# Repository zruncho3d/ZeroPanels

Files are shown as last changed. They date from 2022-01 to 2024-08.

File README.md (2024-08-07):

# ZeroPanels: the sealed, snap-in printer enclosure

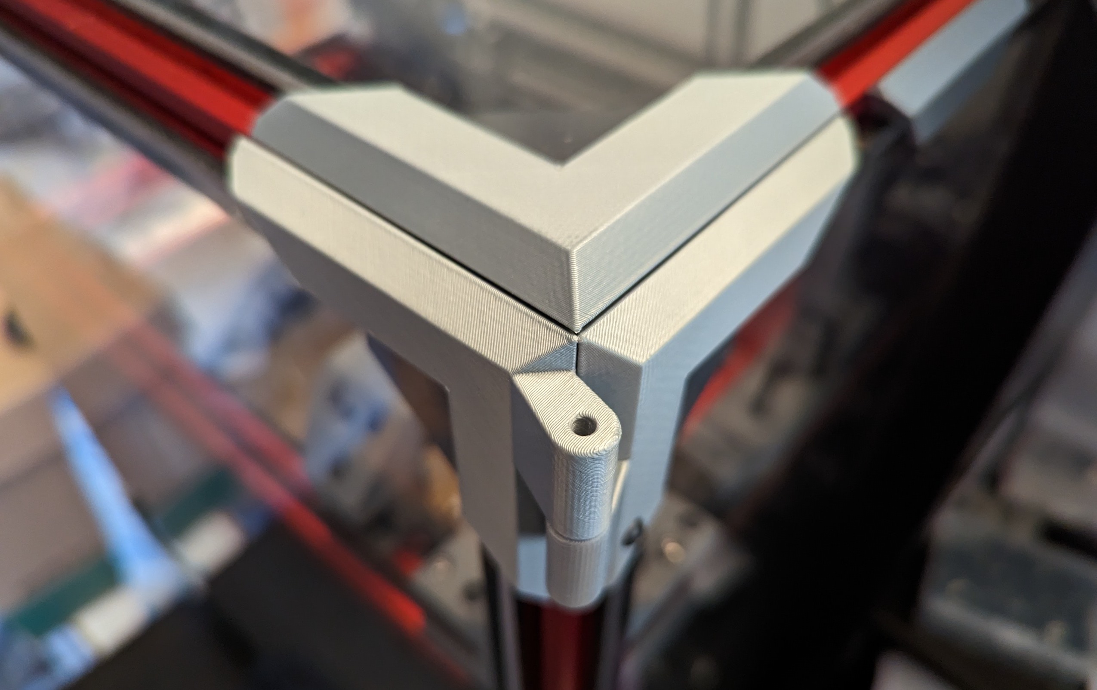
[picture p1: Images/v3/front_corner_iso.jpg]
Iso


**ZeroPanels** is an enclosure design for [Printers for Ants](https://3dprintersforants.com) which makes panel insertion and removal really, really, ridiculously easy.  

The design uses uses screw-less, nut-less, magnet-less, low-infill, 3D-printed clips... and it works with most 1515-based printers, including [Voron Zero](https://vorondesign.com/voron0.2)* (see Compatibility Notes below), [F-Zero](https://github.com/zruncho3d/f-zero), [Tri-Zero](https://github.com/zruncho3d/tri-zero), [Double Dragon (X0)](https://github.com/zruncho3d/double-dragon), [Micron](https://github.com/hartk1213/Micron), [Salad Fork](https://github.com/Yeriwyn/Salad_Fork), [Crucible](https://github.com/Maverick-3D/Crucible), and more.  

**Are ZeroPanels for me?** If you expect to build your printer, then never maintain it or mod it... *move along; these aren't the panels you're looking for*.

But if you've ever had to do maintenance on a printer, or really just enjoying modding and tweaking, then easy panel removal is a godsend, and worth a bit of filament, some tape, and a few magnets.

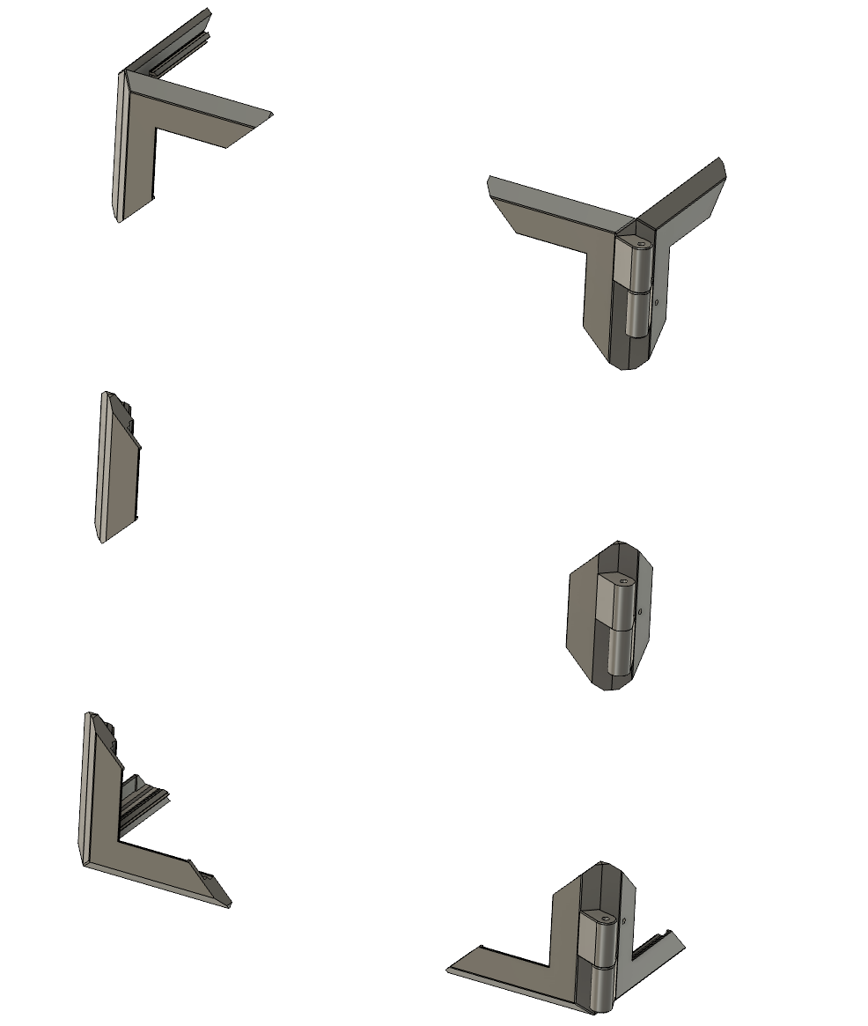
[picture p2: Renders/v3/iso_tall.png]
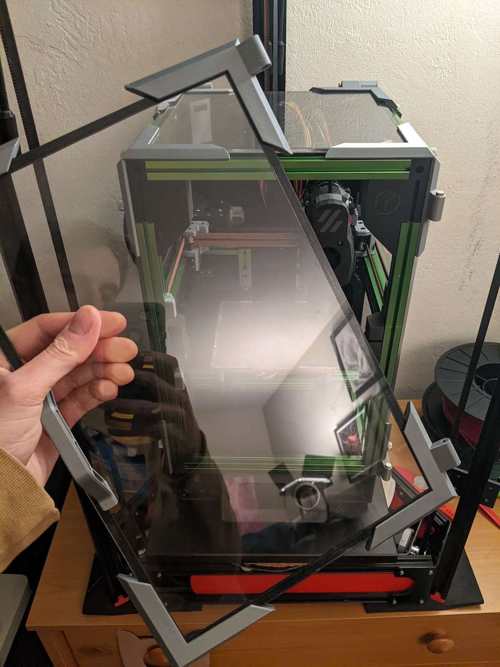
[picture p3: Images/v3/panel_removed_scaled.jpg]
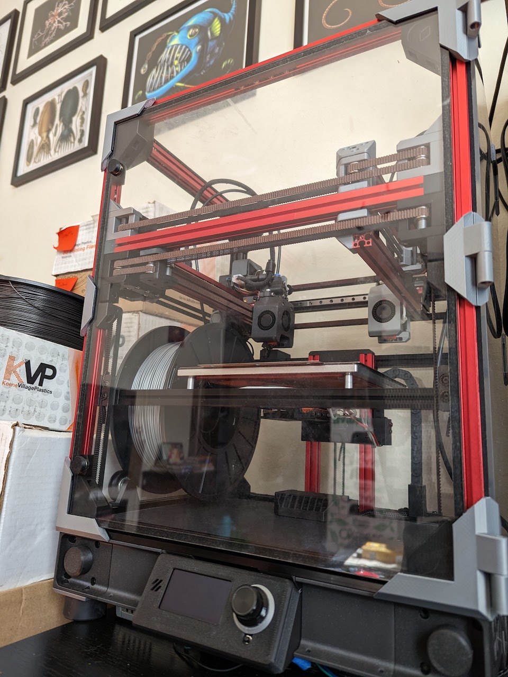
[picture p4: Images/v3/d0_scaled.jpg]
|  |  | 
| - | - | - |
| CAD Render | Zruncho's [Tri-Zero](https://github.com/zruncho3d/tri-zero) + [BoxZero](https://github.com/zruncho3d/BoxZero) w/ZPv3 <p>showing easy door removal and top hinge | Zruncho's [Dueling Zero](https://github.com/zruncho3d/DuelingZero) w/ZPv3 <p>and optional midclips|

**Version 3 adds many meaningful improvements:**
* new "one size fits most" design fits a broader range of panel sizes out-of-the-box
* no need to cut foam tape on a diagonal anymore
* new hinge parts support magnetic and screw-based hinges
* new optional screw lock for hinge bases
* new optional midclips ensure a tight fit with larger panels (like Micron+, Tri-Zero+, Dueling Zero, and others)
* new easier-to-edit, simplified Fusion 360 CAD

The minor downside is that VHB tape is now on the BOM.

[See this video](https://www.youtube.com/watch?v=6F5wUP4zZDg) for an explanation of what's new, with the v3 enclosure on [Dueling Zero](https://github.com/zruncho3d/DuelingZero).

This video is probably the best way to understand what they're like and whether they're for you.

## [> > > Watch v3 update video!](https://www.youtube.com/watch?v=6F5wUP4zZDg)

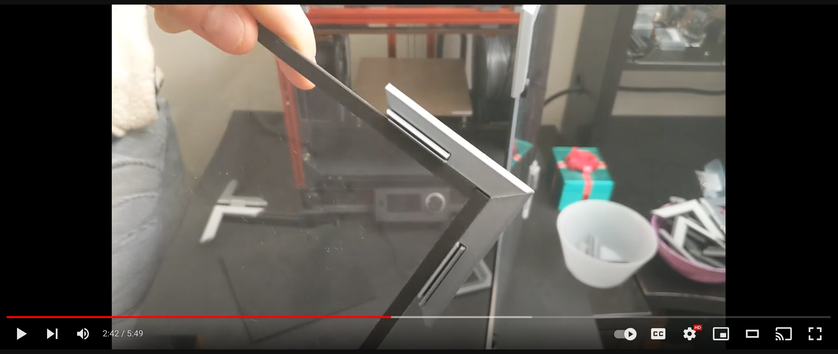
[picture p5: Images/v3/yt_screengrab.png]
(https://www.youtube.com/watch?v=6F5wUP4zZDg)


## [> > > Older v1 video shows fast insertion and removal!](https://www.youtube.com/shorts/L3nBHkO4VzE)

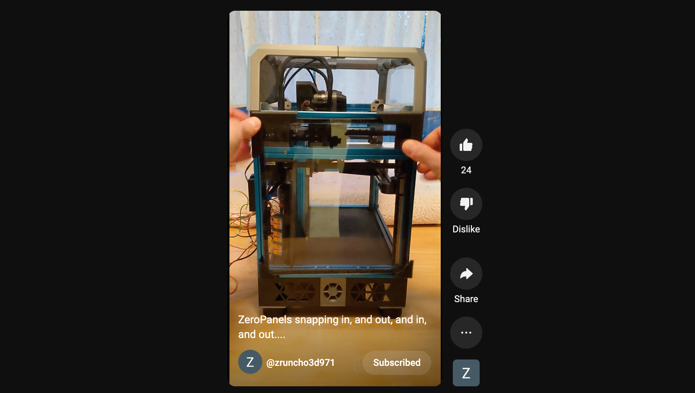
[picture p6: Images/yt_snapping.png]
(https://www.youtube.com/shorts/L3nBHkO4VzE)


## Updates
* 2023-03-05 v3 Release!
* 2022-12-13 v3 Beta program begins on DoomCube Discord
* 2022-04-18  ZeroPanels motivate [BoxZero](https://github.com/zruncho3d/boxzero), a fully-boxed V0 option.
* 2022-03-03 Tecnologic shares ["Tecnologic-style" ZeroPanels](https://github.com/Tecnologic/ZeroPanels/tree/main/Mods/tecnologic/FlyingZero300) for [F-Zero](https://github.com/zruncho3d/f-zero), which have a larger corner size, as well as optional inner parts, and cover all sides.  They're really nice.  They influence v3 and BoxZero.
* 2022-01-23 Public release of original V1 ZeroPanels, which are intended mostly for just the left and right sides of a printer, and assume a tophat on top and a default V0 hinged front panel.

## Why ZeroPanels?

**No !@#$ing screws and nuts.** A default V0 enclosure (just left & right) requires 24 screws and nuts. Even with [NoDropNuts](https://github.com/zruncho3d/f-zero/tree/main/STLs/NoDropNuts) to hold the nuts in place, having to unscrew a bajillion screws to remove one panel - and then screw them all back in again - is not fun.

**Mind the gap.** Many [Printers for Ants](www.3dprintersforants.com) need an extra mm to clear an MGN7 carriage (17mm wide) when mounted inside a 1515 extrusion.  You can solve this problem by printing thicker clips and using foam tape, but if you’re going to reprint enclosure parts… you might as well avoid the pain of all those screws too.

**Seals tight.** This gap is closed by foam that you add to the panels, and the extrusion clips gently press the foam against the panels.  Speaking of which...

**Shut the front door.** ZeroPanels are sealed by default, including the front door.

**Bye-bye, tophat.**  Easily add a top-hinge panel to replace a tophat on for fully-boxed printer mods like [BoxZero](https://github.com/zruncho3d/boxzero).

**ZeroPanels FTW.**  There’s more thought and work in these little parts than you might realize.

## Bill of Materials

| Part/Material | Description | Amount | Link | Note |
| - | - | - | - | - |
| Filament | Something strong and slightly flexible | - | - | Tested with ABS, though PETG probably will work, too.  PLA is probably not a good fit here. |
| Foam Tape | 3mm or 1/8" Adhesive-backed Foam Tape | Enough to cover all panel edges | [example (Amazon) ](https://www.amazon.com/gp/product/B08MTXJBR5/ref=ppx_yo_dt_b_search_asin_title?ie=UTF8&psc=1) | The Yotache brand is nice, because it doesn't show lines on the adhesive side through the acrylic, unlike others. |
| Tape | Double-sided VHB tape (1mm-ish) | Some | [example (Amazon)](https://www.amazon.com/gp/product/B09R5ZF8XZ/ref=ppx_yo_dt_b_asin_title_o01_s00?ie=UTF8&th=1) | Doesn't need to hold *that* well; non-genuine VHB is probably fine. |
| Magnets | 6mm dia x ~3mm depth "V0 standard" magnets | 6 per hinge pair | Some | See "Choosing a Hinge" below |
| Screws | M3x35 SHCS/BHCS | 2 per hinge pair | Link | See "Choosing a Hinge" below |
| Screws | M2x12 self-tapping screw (or M2x10 in a pinch) | - | (optional) 1 per hinge | Optional screw lock.  Can also drill out the hole and use an m3 screw too, if the hole strips, or you just want an m3. |
| Nuts | M3 regular or Nylock nut | 2 per hinge pair | Link | See "Choosing a Hinge" below |
| Panels | 3mm | Depends | - | These should be sized for ~6mm beyond the inner frame width.  For example, on a V0, 200mm + 6mm * 2 --> 212mm width.  *Note*: the front door becomes the same size as the side panels, so a V0 panel kit with tophat needs a 9mm shave on the top to fit here.|

**Choosing a Hinge**: magnet or screw?  You can do one of each; Zrucho's preference is a screw-hinged top and magnet-hinged front.  You can even skip a top hinge and just use a snap-in top panel, especially if you want to flip your printer and have it sit on a flat surface frequently.

The magnet hinge enables you to grab the front panel, lift up, and remove it entirely.  The screw option enables you to tighten the screws, so that the top panel holds in place vertically, for extruder access or filament changes.

If you want a nice strong front-door close, then add 2-8 optional door magnets. The printed parts match the ZeroPanels offset, but also give a more powerful seal.  The front-door bits require a few extra parts:

| Part/Material | Description | Amount | Link | Note |
| - | - | - | - | - |
| Screw | M2x10 self-tapping screw | - | 1 per unit | Longer lengths can typically be cut down to size with strong wire cutters. |
| Screw | M3x6 FHCS | - | 1 per unit | |
| Tape | Thin double-sided tape, 1/4" / 6mm wide | - | Enough to cover one magnet per unit | Cut any size width you have to size. |
| Magnet | 1/8" thick, 3/8" diameter countersunk ring magnet | - | 2 per unit | Choose your preferred size |
| Magnet | 1/8" thick, 1/2" diameter countersunk ring magnet | - | 2 per unit | Choose your preferred size |

## Printing Tips

The unusual 45-degree orientation is what makes these possible.

For **non-hinge** parts:
* 0% infill (minimum), 2 perims (minimum), 2 bottom layers, 5 top layers, 0.6 forced width, 0.2 layer height

The wider extrusion width helps with the overhangs.  However, if you get too much corner curl with the wider width, try 0.45 or 0.5 width instead, possibly with an extra perimeter, and/or reduce the layer height to 0.16mm.

For **hinge** parts:
* Same params, except use 16% infill (minimum); extra perims may improve hinge strength too

Bed adhesion is important for a cantilevered part like this.  Consider all of these:
* a hotter heated bed
* a properly prepared PEI surface (soaped, scuffed, iso'ed)
* extra first-layer squish
* an adhesion aid like Vision Miner Nano
* brim, if still stuck

If there's an interference with the extrusions, then you'll need to fix it in CAD beforehand (using a press-pull operation is easy enough...) or use flush cutters after.  Sorry, but generating and orienting versions of every part for every printer is a maintenance burden.

Get the settings right, and each part should look perfect, even when printed at the flowrate limit of the hotend.  The sample parts below show v1 parts in KVP Stellar Black ABS, printed at 235C on an [F-Zero](https://github.com/zruncho3d/f-zero).

Print Sample

## Instructions

### Required Reading: understanding the thickness setting

**Always print and assemble a test panel first, because component thicknesses vary.**  

Acrylic panels, extrusions slots, foam tape, and VHB tape all vary slightly in thickness, as does each printer.  You want to ensure that these parts work for your printer, *before* printing a full set.

The default panel set assumes these sizes:
* VHB tape thickness: 1.1mm
* acrylic panel thickness: 2.9mm
* foam tape thickness: 3.0mm

This stack needs a tiny bit of squish to form a good seal.   If that stack is too skinny for the plastic part, an air gap will result.  If that stack is too thick, the tape near the hinges may separate over time, and a gap may form in the center of the panels due to bowing.  In a hot chamber, your panels might even set into a bowed position.  

By default, the stack assumes a 7.0mm stack thickness, squeezed down to 6.7mm, ensuring about 0.3mm of squish.

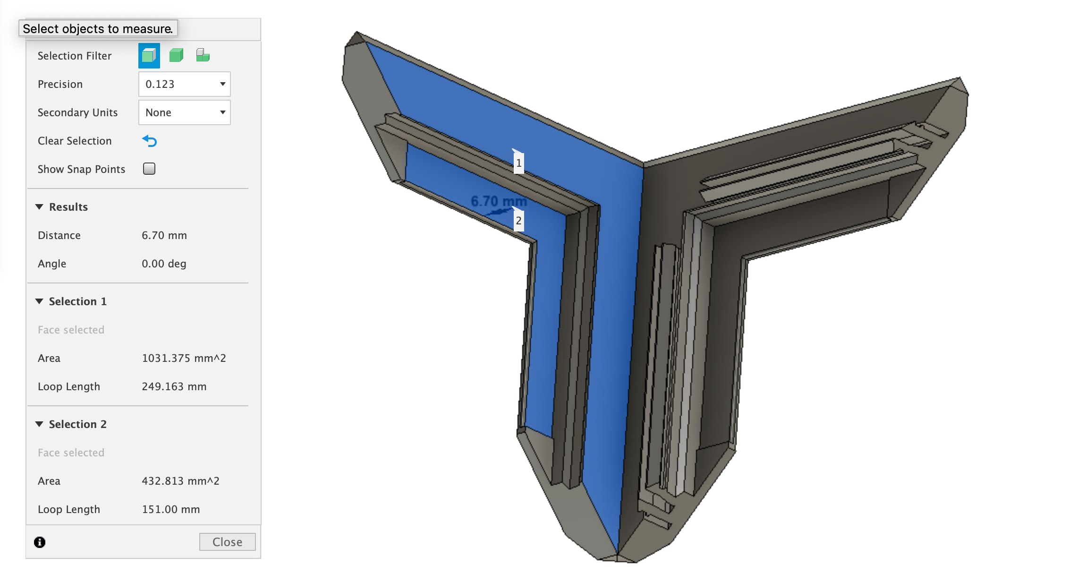
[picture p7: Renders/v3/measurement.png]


These numbers are based on the collected measurements from the many beta testers, in an attempt to provide a single reasonable default.

The amount of "extrusion grip" has been set similarly, to a size that should fit most extrusions and provide a reasonably satisfying, audible click, especially with LDO and MakerBeamXL extrusions.  Misumi are known to have wider slots, but you can somewhat account for this by offsetting the attachment of the corners to the panel, to effectively preload them, plus the screw locks for the hinges help here too.

If your component stack is less than 6.8mm or more than 7.2mm or so, then you're more likely to benefit from a custom size. However, if you need a size tweak, it's a straightforward change in the Fusion 360 CAD, as noted below.  **Try it first.**

### Print and assemble a test panel

#### Print and prep corners

Print 4 normal corners, using the settings above.

For each piece, cut out VHB to fit, with 90 degree cuts only, for all areas that will touch the panel.  Use two pieces for the L shapes and 1 for the straight-through mid-pieces, as shown below.

Push the tape downwards, and ensure it sits perfectly flat, or reapply the tape and try again.  A printer spatula works great for this purpose.  Looks like this:

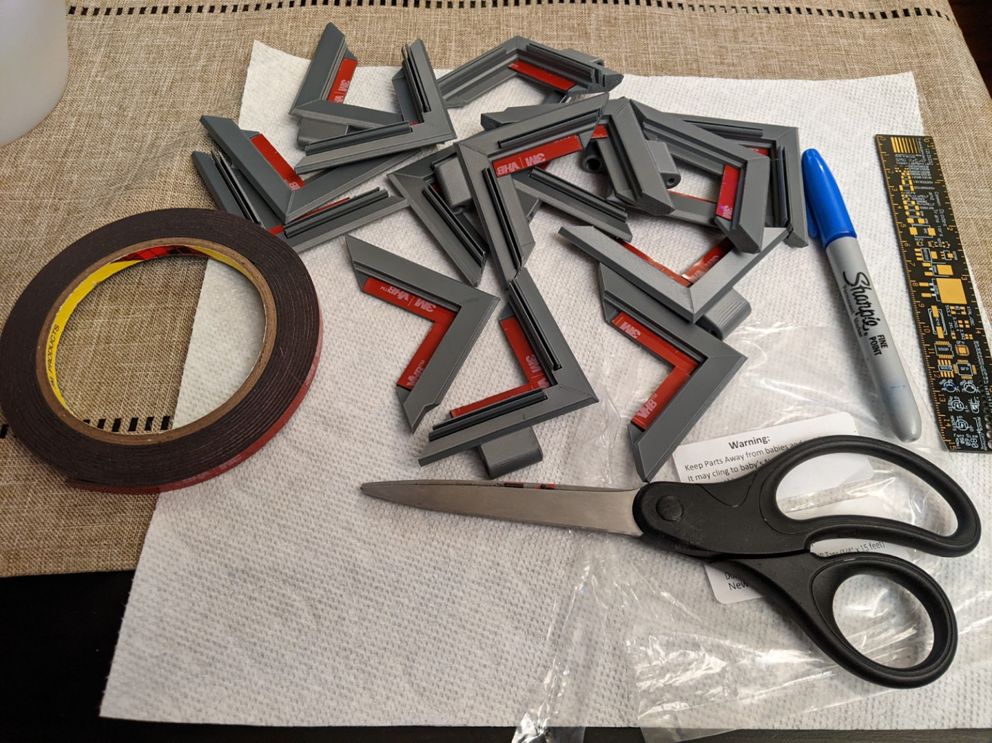
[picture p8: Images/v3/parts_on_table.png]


#### Prep panel with foam tape

You can do this while your parts are printing.

Remove a panel’s length of foam tape.  Get it started at one end, then *very gently* apply a bit of tension on the tape; run your finger along the panel edge and the tape edge.  You can get a perfectly-straight application with this technique, and by not pulling too hard, you prevent ugly stuff from showing on the tape's underside.  Just make sure everything overlaps.  

Repeat for the other 3 parts to complete a panel.

Make sure to remove the acrylic panel backing first!  You can remove just the edge part to keep the panel pristine.

Then put a book on top and let it sit foam-down for a bit.  Otherwise, expect that the tape might peel up near the edges, where you’re likely to have touched it the panel with your finger oils.  You want the tape to set a bit.

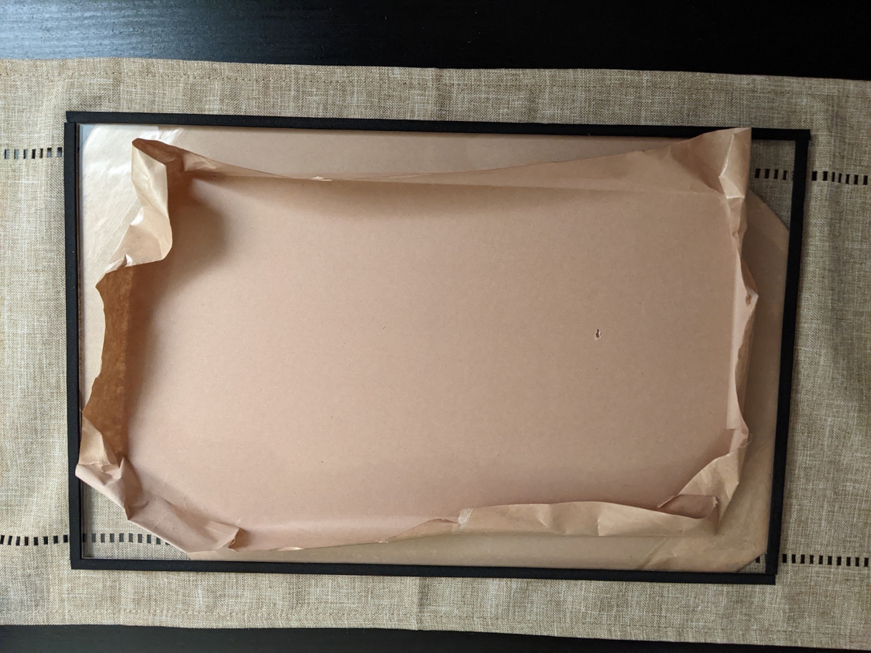
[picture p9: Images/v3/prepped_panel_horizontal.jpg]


#### Pre-test the panel

Make sure there are no occlusions before trying this - that is, there are no clips interfering with printed parts, and no nuts where the panels will insert.  Trim the clips if there are any occlusions.

Add all 4 clips with the red VHB backing still in place, to confirm that the stack height is about right.  Make sure the panel grips into the extrusion slots. The panel should hold securely, but remove easily when you push out from the inside, one corner at a time.  It's kinda like removing car interior pieces with plastic clips.  

Now, do the real test.

#### Assemble the panel

Remove the VHB's remaining red backing on the 4 clips. This step can be surprisingly hard if the backing sticks well to the tape itself.  Here's a protip: using a thin flat printer spatula, separate a corner of the backing from the tape.  As soon as you have a little triangle to grab, use needle-nose pliers to grab the tape and slowly peel back.  You can use this trick to avoid disturbing the VHB and having it peel away from the part.

Next, secure one plastic corner to a panel corner.  Mark the corner, say, with a Sharpie on the inside.   Squish it HARD.  Align the panel to the printer.  Do the same for the opposite corner, being careful to align it all to the extrusions.  Squish it hard.  Then add the other 2 corners in place.  To help ensure the VHB sticks as well as possible, you can pop off the panel and have some books weigh it down.  Make sure it has time to set before doing insertion/removal testing.

#### Check the fit

Look from the side, using a phone flashlight, to ensure no air gaps are present.  The panel should seal.  If it bows outward, consider using the optional mid-clips and mid-hinge for additional hold.

See if the amount of snap feels right.  See whether the assembled panel holds steady once inserted, and whether it removes with an amount of force that works for you.

**All good?**  Print the rest.

### Print the rest

#### Assembling magnetic hinges



These are simple, easy, and fast to build.

First, make a magnet pair for each hinge: literally, a pair of glued magnets with some CA glue.  It's out-of-chamber, so regular glue is fine.

Put a spot of glue into the hole on the fixed part, where the magnet pair will go; for the door, these would be on the right, and are the parts with a hole for an M2 locking screw.  Push the magnet pair in and make sure it sits flat.  Yes, a whole magnet sticks out.

Now, get the moving part, the one without a hole, with a deeper pocket.  Clean up the hole beforehand with a 6mm diameter reamer, end mill, or M6 screw.  Everything is glued here and non-critical, so a little looseness in the magnet pockets is fine; you just need the magnet to insert and remove easily, plus have space to act as a hinge.  Put a spot of glue in this part.  Then add a magnet onto the magnet pair of the fixed part from before, and press this into the pocket, just enough to become obscured.  Slide it out carefully, then press down all the way with a pen or other plastic thing that fits, until it sets from the glue.  

Test the hinge!  It should pop on and off without issue and rotate easily.  With two, the rotation will be even smoother.

#### Assemble the door

Assemble two hinge pairs and complete the right-side panel.  Attach the right-side panel and lock it in place with the M2 locks near the hinges.   Turn the screws until they hit the end and resist, but DO NOT strip them.  The screw locks don't need to be super-tight anyway; they're mostly preventing the panel clips from unclipping, vs actively pressing against the extrusion slot.  Worst-case, if you strip these, you can remove a chunk of panel clip, drill them out to m3, and have them mate to a nut in an extrusion slot.

Then assemble the door panel, ensuring that you use smooth corners, and add it.  You *can* use the panel clips everywhere, including as a door closure, but given the high cycle life there, magnetic feels right... it has an infinite cycle life.

The door should pop on and off easily.  To reattach, push the door against the front, then let it fall down into place.

Once it's in place, consider printing and attaching the optional-but-recommended magnet bumps, which cover up cylinder or ring magnets, and which grip tightly to the corresponding magnet receivers that clip into the extrusions.  The bumps attach using thin (0.1mm or so) double-sided tape.

Two magnet bumps on the left of the door is a good start, with others on top and side if you see air gaps or want a generally tighter seal.  Use more for bigger panels, too, especially for T0+ or D0-size printers.

#### Assemble a screw-based hinge (especially on top)

Similar steps here. The screw top will be exposed on the top side (assuming the door orientation), and a nylock nut goes into the pocket, and is hidden.  Tighten both screws fully only when the top and back are in place, along with the M2 screw locks on the top rear.

You can go tight enough for the hinge to hold vertically in place.

### Troubleshooting Tips

**Cooling a problem?**  Print the full plate or space out the parts on the plate.  Print thinner layers, print slower, and print cooler.

**Adhesion a problem?**  Add a brim, add more first-layer smush, print thinner layers, or use a bed adhesive.

**Strength a problem (breaking at layer lines)?**  Reduce cooling, add an enclosure, or jack up the print temp.  These are functional parts and should always be printed hotter if possible, for strength.

## CAD Notes

The CAD is designed to be understandable and modifiable, so you can do your own customizations, if not a CAD expert.

All sketches, operations, and construction planes are labeled.

Almost all dimensions of value are stored as parameters.  Here are the most useful ones:

`foam_tape_compressed_thickness`: adjust this from the default size for your stack
`no_grip_len`: increase if you want more length without a clip
`main_corner_len`: increase to 80 if you want a longer clip

Other params don't affect the corners, but make it easy to set the distances to match your printer, for easier CAD import.

Once you've made your adjustments, you'll need to export all bodies, reorient on the 45, and face all seams face backwards so that they end up hidden.

## Compatibility notes

(1) The latest [Voron Zero](https://vorondesign.com/voron0.2) (0.2) needs flat top chops on the corners for extrusion tophat compatibility (so that the clips don't interfere with the tophat plastic parts).  For compatibility with a full-height front, like those found in most V0 frame kits, you'd need to also mod the front clips a bit, since the plastic would be in the way of the top 9mm and bottom 9mm of acrylic panel.

(2) The original Dueling Zero README lists panels that are 9mm beyond the inner frame width, not 12mm.  To use these on D0, make sure to adjust the magic 'x' parameter and follow the note in the CAD, then export the parts you need.  If you go for normal-size frames, then ignore this message.

## FAQ

### What's the catch?

Because the clips enable the panels to float, the panels provide no rigidity benefit to the frame, just like [curtain walls](https://en.wikipedia.org/wiki/Curtain_wall_(architecture)) on modern skyscrapers.

However, because these panels aren't positively coupled to the frame, they may reduce noise, to make it less likely that they act as a speaker to amplify resonances.

We'll see about that one.

Another possible catch is that not every printer is dimensionally accurate, and that can affect how well the design works *for you*.  They're designed to account for variance in panel width, extrusion slot width, and panel thickness.  But if your printer prints bulges at the corners, for example, the clips may not work for you.

### Could I extend the design to fully cover extrusions?  Yes.
Yes, you could!  See the [Technologic-style version](https://github.com/Tecnologic/ZeroPanels/tree/main/Mods/tecnologic/FlyingZero300) for an example.

You'd have to think through the print orientation(s) though to fully reuse this profile.

### Can I do a double-panel version?  Yes.
Definitely.  You'd need to thicken the panels, but add an extra layer of VHB and another panel and make small mods and you may be able to do a simple double-panel setup.

## Credits

These parts are a spinoff from the [Tri-Zero](https://github.com/zruncho3d/tri-zero) project.

V3 credits:

Thanks to Grizzle357, sorkyl, Floaf, falo, SuperPringles, burningBeard, Ax4x Se7en, John, Kosh42EFG, schwaded, and Bacon for taking measurements that informed the parts here.  Thanks to chadonka for printing an entire enclosure on an in-progress D0!

V2 credits:

Unreleased, but inspired by Tecnologic.  The CAD got out of hand and needed to be redone properly, starting over from the first sketch.

V1 credits:

Thanks to Yeri, Speedy, Ericsson, RogueNeurons, Maverick, Sparkss, rok3, flyespresso, tecnologic, and Lowstream on the [DoomCube Discord](https://discord.gg/doomcube) for extrusion measurements.

Thanks to Ericsson, RogueNeurons, Maverick, Yeri, rok3, flyespresso, StoicHollow, Lowstream, and Tigran on the [DoomCube Discord](https://discord.gg/doomcube) for sharing test-print feedback!

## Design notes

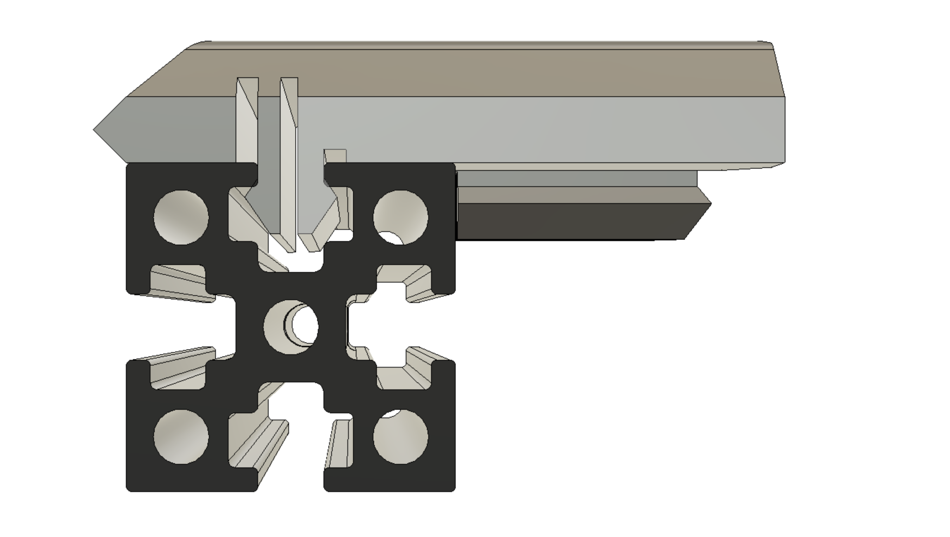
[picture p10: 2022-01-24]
Renders/side_view_perspective.png

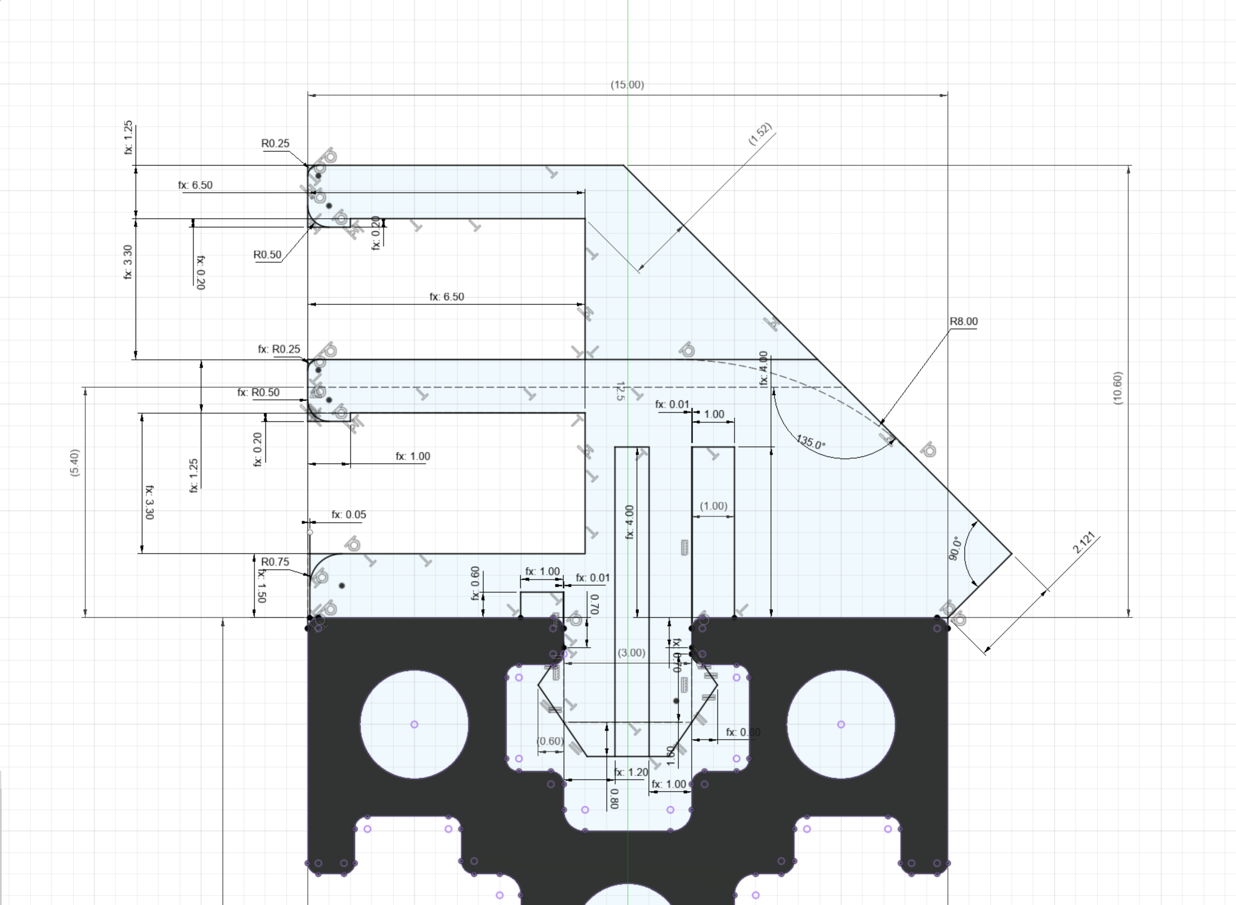
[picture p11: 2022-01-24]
Renders/sketch.png

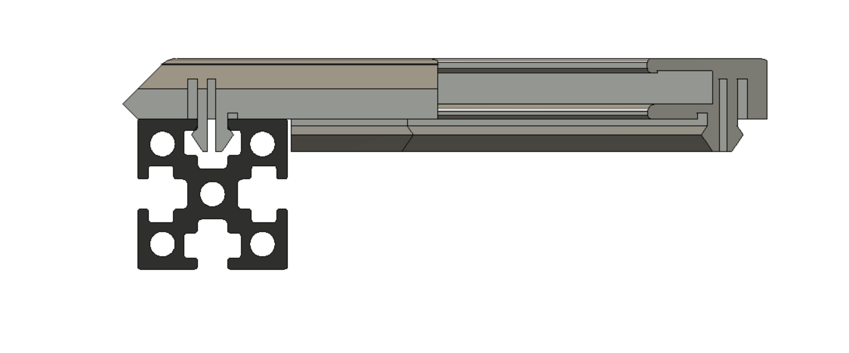
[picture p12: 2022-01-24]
Renders/side_view_ortho.png

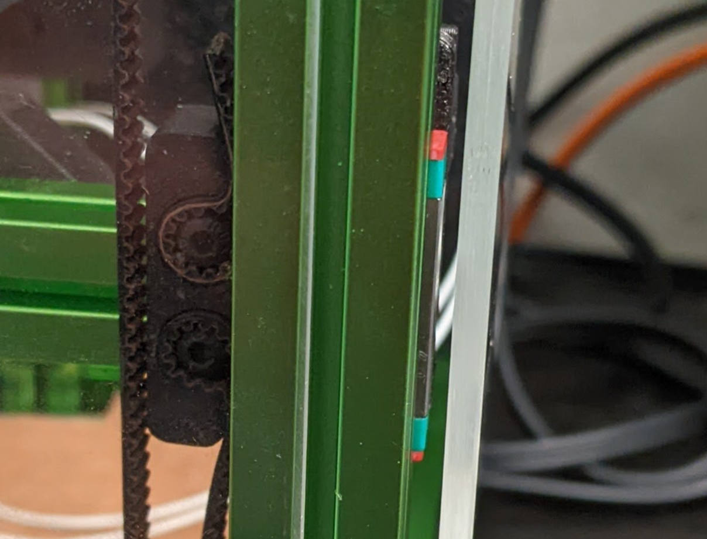
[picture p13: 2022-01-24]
Images/T0_filling_the_gap.png

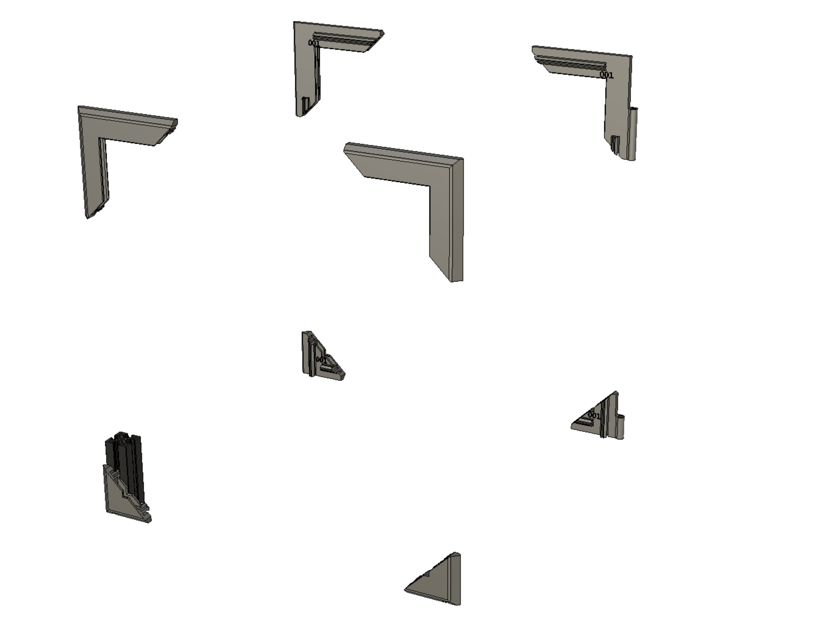
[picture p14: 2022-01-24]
Renders/all_in_iso.png

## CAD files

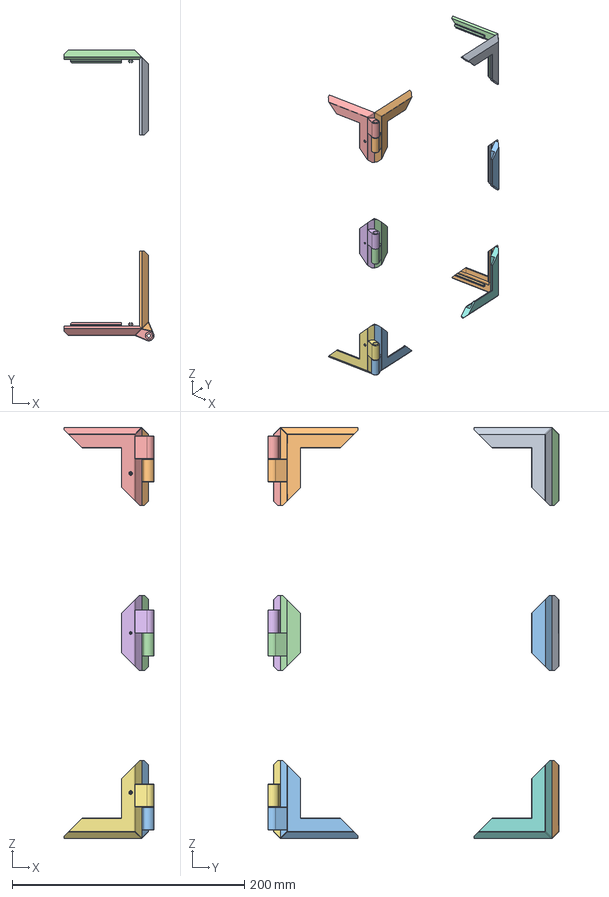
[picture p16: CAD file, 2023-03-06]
CAD/ZeroPanels_v3_2023_03_05.step
77.6 x 250.6 x 354.2 mm

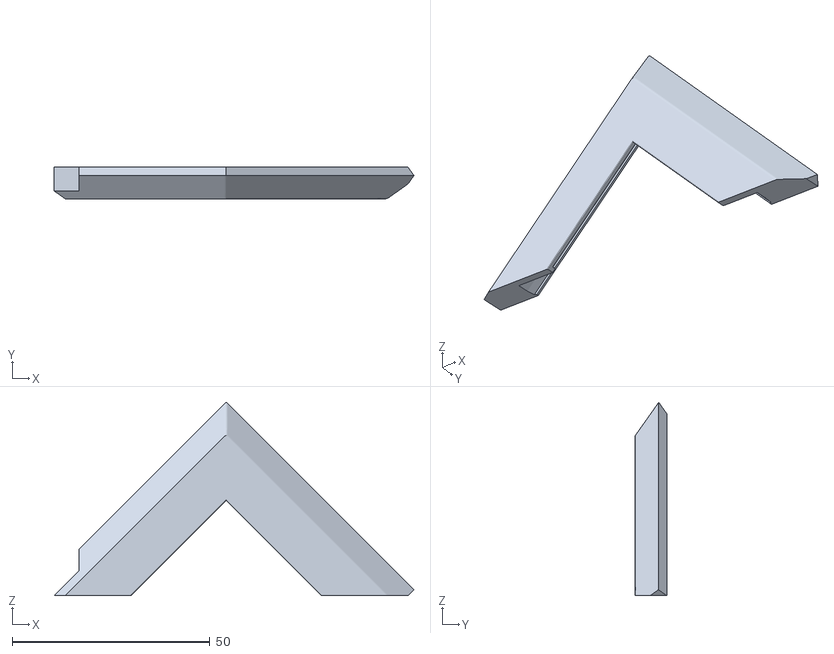
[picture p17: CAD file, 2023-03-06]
STLs/v3/optional/zp_smooth_bottom_12864cutout.stl
90.9 x 8.00 x 48.9

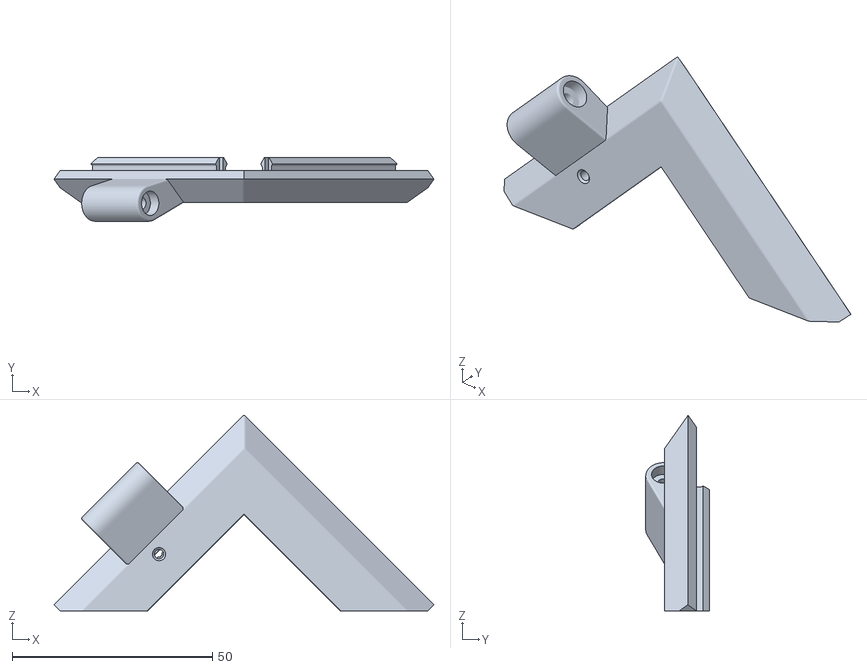
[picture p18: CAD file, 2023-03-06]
STLs/v3/zp_hinge_top_fixed_x2.stl
94.9 x 15.9 x 48.9

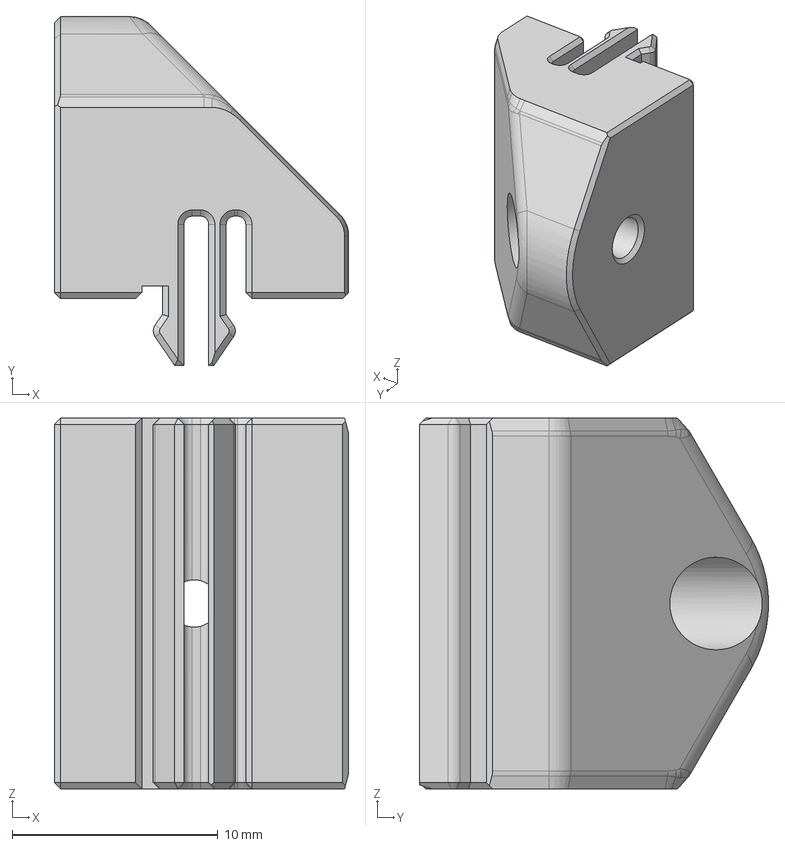
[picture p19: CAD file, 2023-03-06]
CAD/Magnet_Receiver.step
14.3 x 16.9 x 18.0 mm

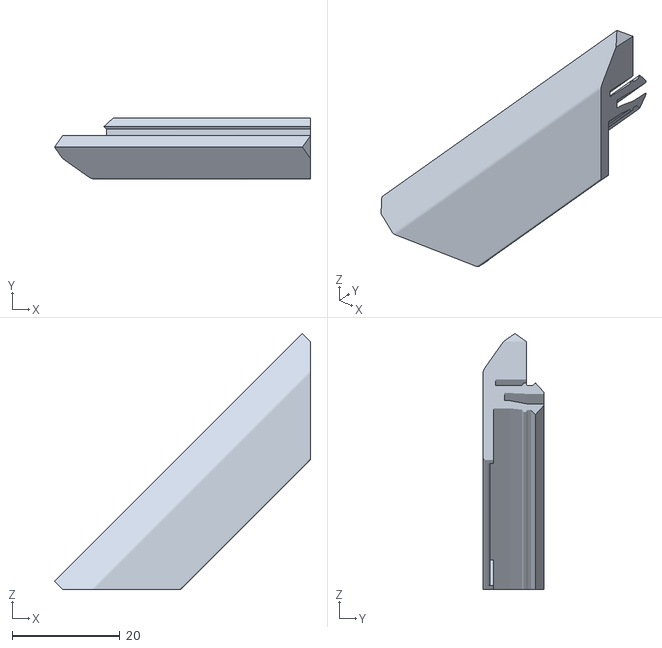
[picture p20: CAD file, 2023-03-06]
STLs/v3/optional/zp_midclip_optional_x5.stl
47.5 x 11.3 x 47.5

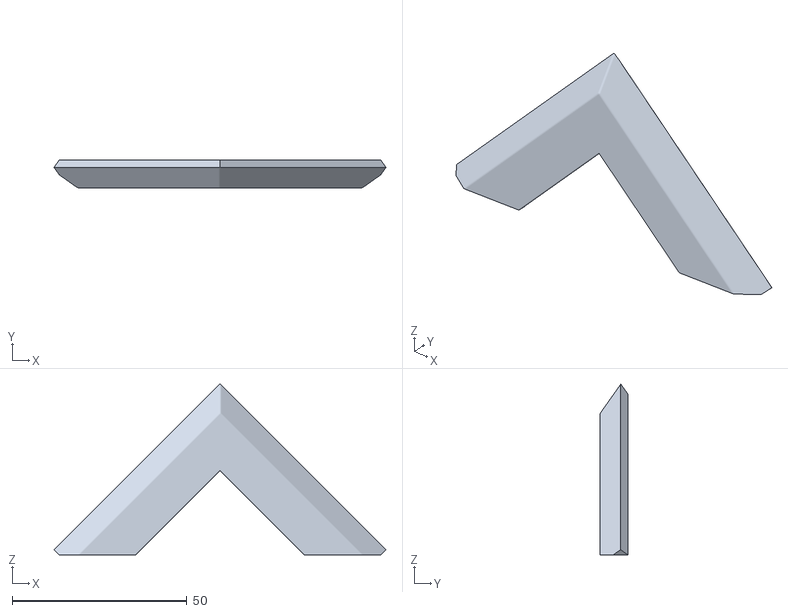
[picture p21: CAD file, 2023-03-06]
STLs/v3/zp_smooth_x2.stl
94.9 x 8.00 x 48.9

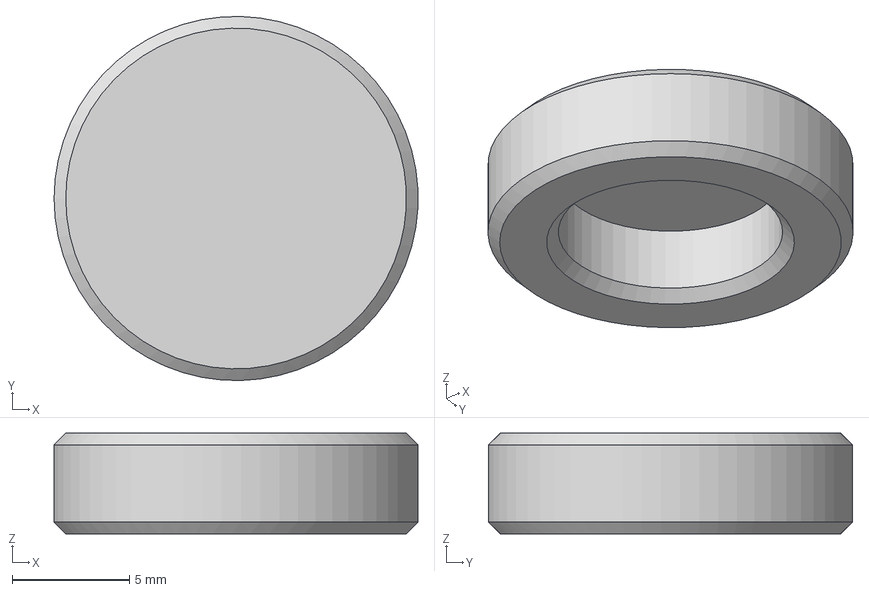
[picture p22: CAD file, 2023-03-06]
CAD/Magnet_Bump.step
15.5 x 15.5 x 4.30 mm

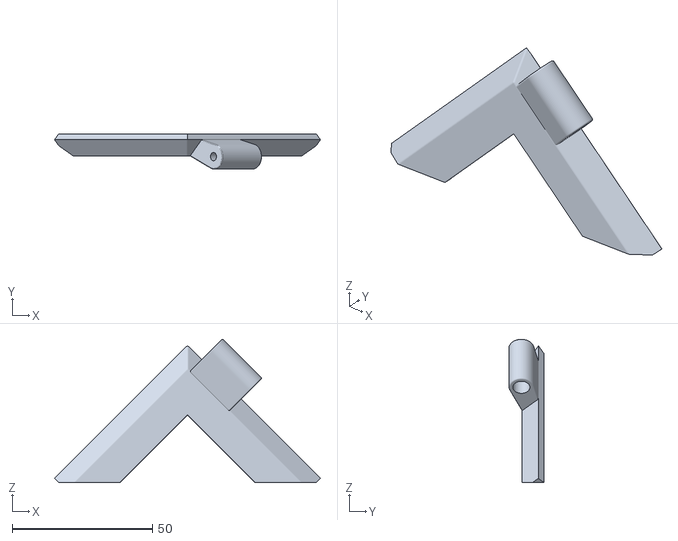
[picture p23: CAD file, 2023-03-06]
STLs/v3/zp_hinge_top_moving_x2.stl
94.9 x 12.6 x 51.2

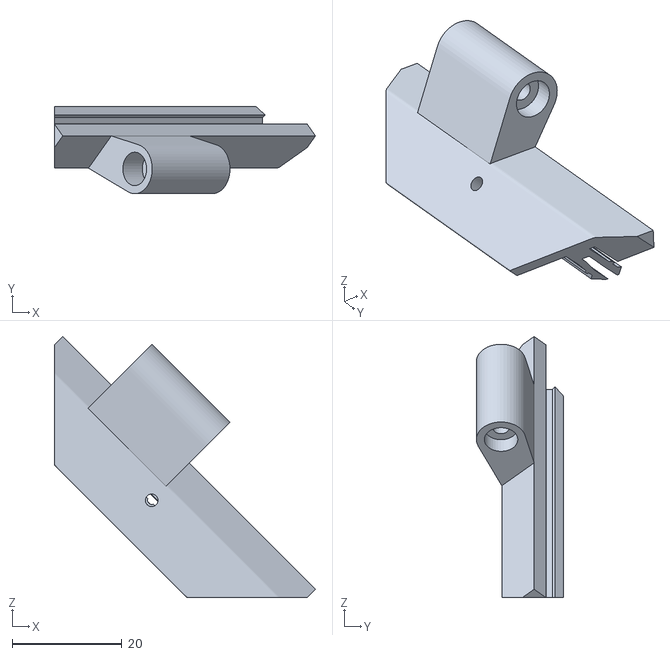
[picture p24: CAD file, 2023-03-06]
STLs/v3/optional/zp_hinge_middle_fixed_optional.stl
47.5 x 15.9 x 47.5

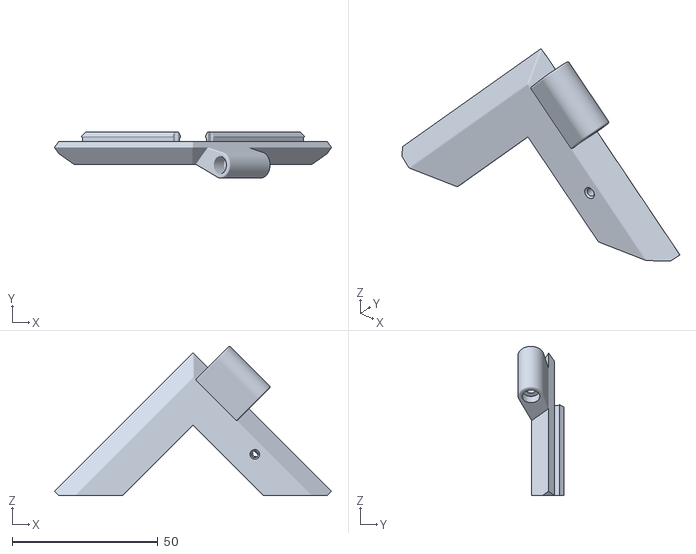
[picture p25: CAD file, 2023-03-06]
STLs/v3/zp_hinge_bottom_fixed_x2.stl
94.9 x 15.9 x 51.2

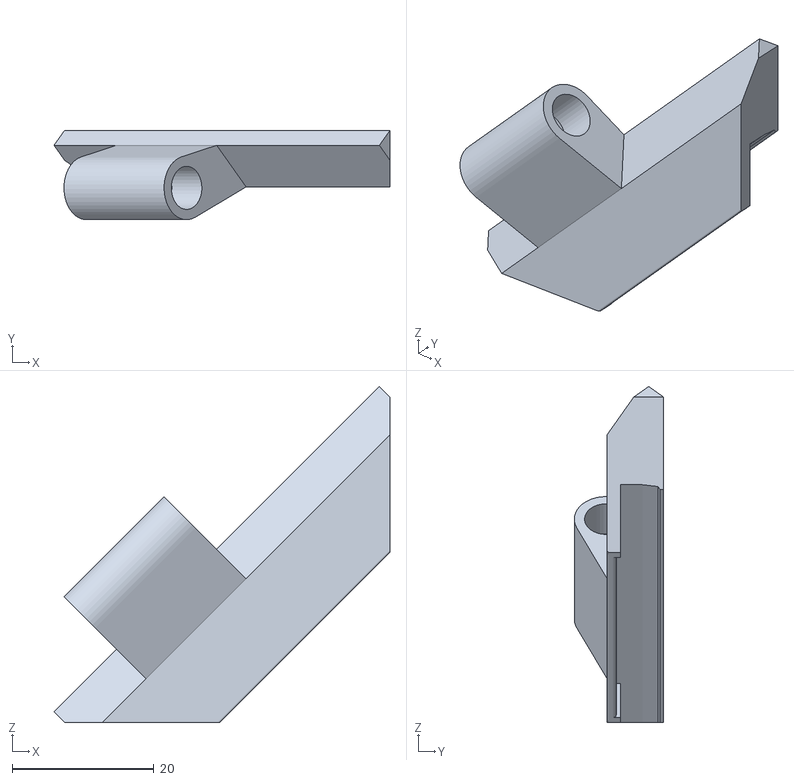
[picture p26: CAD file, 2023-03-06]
STLs/v3/optional/zp_hinge_middle_smooth_optional.stl
47.5 x 12.6 x 47.5

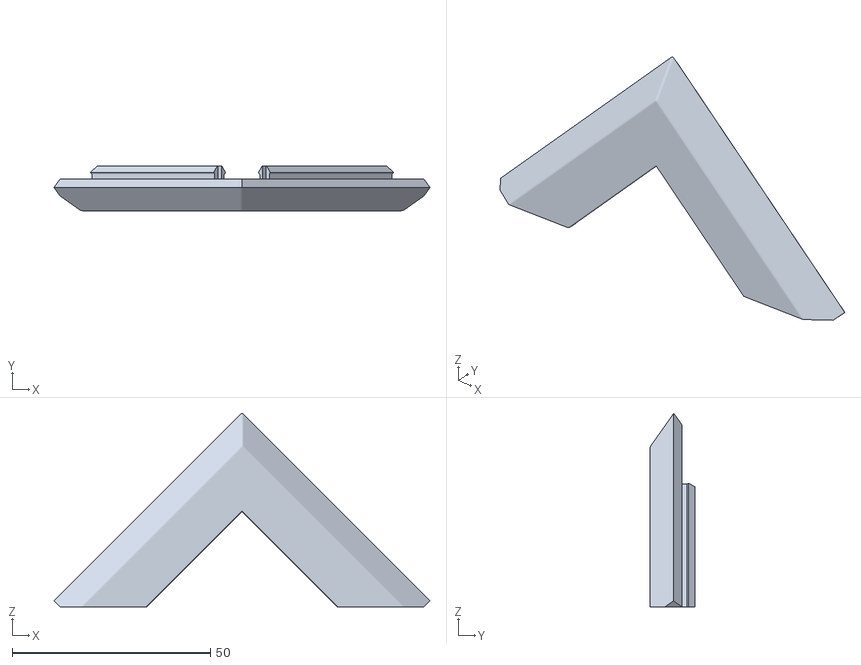
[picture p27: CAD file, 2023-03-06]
STLs/v3/zp_clip_x8.stl
94.9 x 11.2 x 48.9

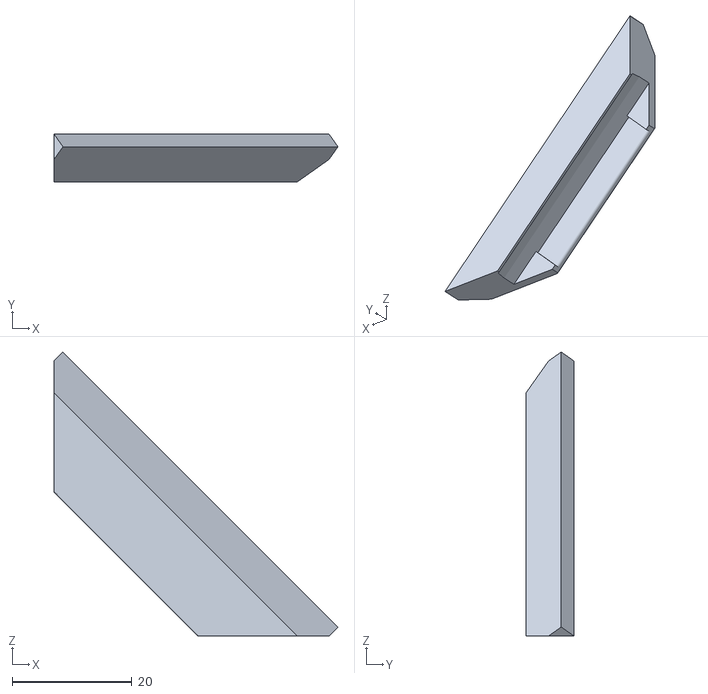
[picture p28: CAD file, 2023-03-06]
STLs/v3/optional/zp_midclip_smooth.stl
47.5 x 8.00 x 47.5

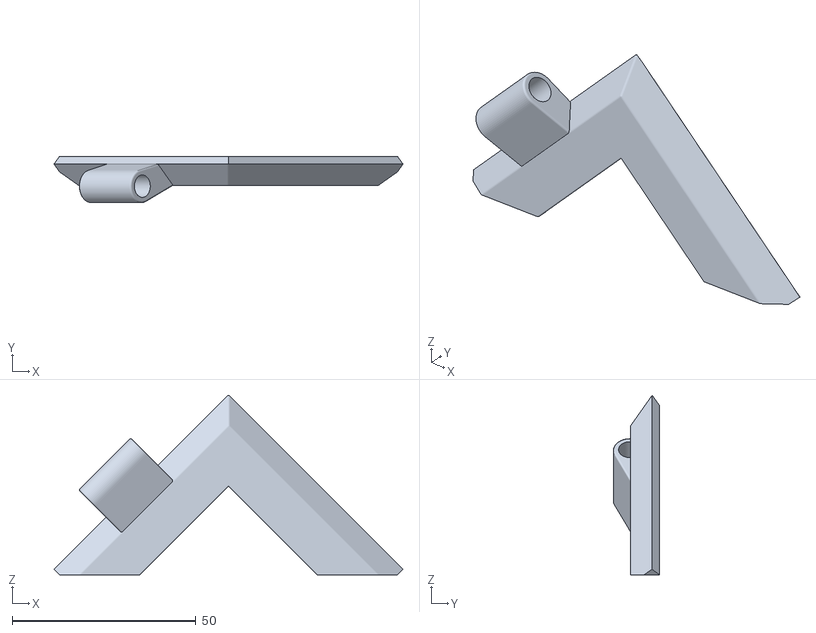
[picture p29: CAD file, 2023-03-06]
STLs/v3/zp_hinge_bottom_moving_x2.stl
94.9 x 12.6 x 48.9

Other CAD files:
STLs/v3/optional/magnet_receiver.stl
STLs/v3/optional/zp_hinge_bottom_moving_12864cutout.stl
STLs/v3/optional/magnet_bump.stl
STLs/Archived/Parts/General/General_015_Left_Front_Top_Right_Rear_Top_Clip_x2.stl
CAD/Archived/ZeroPanels_2022_01_23.f3z
CAD/Magnet_Bump.f3d
CAD/Magnet_Receiver.f3z
CAD/ZeroPanels_v3_2023_03_05.f3z
STLs/Archived/Parts/General/General_001_Left_Front_Bottom_Right_Rear_Bottom_Clip_x2.stl
STLs/Archived/Parts/General/General_001_Left_Front_Top_Right_Rear_Top_Clip_x2.stl
STLs/Archived/Parts/General/General_001_Left_Rear_Bottom_Clip_x1.stl
STLs/Archived/Parts/General/General_001_Left_Rear_Top_Clip_x1.stl
STLs/Archived/Parts/General/General_001_Right_Front_Bottom_Clip_Hinge_x1.stl
STLs/Archived/Parts/General/General_001_Right_Front_Top_Clip_Hinge_x1.stl
STLs/Archived/Parts/General/General_015_Left_Front_Bottom_Right_Rear_Bottom_Clip_x2.stl
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

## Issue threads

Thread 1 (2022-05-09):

Any way to mount the back panel using these parts?

bassamanator, 2022-05-09:
I'd like to mount my Voron 0.1 back panel using this design, but it seems this will only work for the size panels?

Interesting design. Thanks!

zruncho3d, 2022-08-30:
(just seeing this now)

You can lift the back panel up and it should still seal, at least using Tecnologic-style panels (a larger variant I really like).  More here:
https://github.com/zruncho3d/BoxZero

You may need to add some foam tape to the back, by the motors/umbilical plate though, but you shouldn't need a larger plate.

Closed 2022-08-30.

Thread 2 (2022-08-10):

Insulation

taihon, 2022-08-10:
Hello. First of all - thank you for this mod :) It's fast to print and beatiful to look at.
In the FAQ section you've mentioned "clips enable the panels to float". How would i go about insulating v0 chamber then?

taihon, 2022-08-10:
To anyone who comes here in the future - we're supposed to put foam tape on panels inbetween clips, as usual.

zruncho3d, 2024-08-07:
Yep

Closed 2024-08-07.

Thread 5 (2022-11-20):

Can't slice the files.

Neiizo, 2022-11-20:
Well.... I have posted this with no text by mistake...
I wanted to print this, but for some reasons, I cannot slice the part. I am trying to print the v0 15 parts plate. I am using superslicer. I have heard on discord I am not the only one having this issue. any clue why?

EDIT: I have found the culprit: I cannot set 1 perimeter at 0.7mm wall thickness

Neiizo, 2022-11-20:
Well.... I have posted this with no text by mistake...
I wanted to print this, but for some reasons, I cannot slice the part. I am trying to print the v0 15 parts plate

Closed 2024-08-07.

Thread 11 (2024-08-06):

2020 slot 5 version?

Jomik, 2024-08-06:
Hey! This looks really awesome, would love to use it on my printer.
It is a 2020 with a 5mm slot from [motedis](https://www.motedis.dk/en/Aluminium-Profile-20x20-I-Typ-slot-5).
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

I looked into the CAD, but sadly I can't really see a good way for me to adapt this? Can you enlighten me on what I would need to change? Or if it's an easy change for you, I'd love a version! :)
I hoped for it to just be two variables 🙈

zruncho3d, 2024-08-07:
Newer CADs of mine explicitly parameterize the extrusion size, but this one predates that.

To generalize this to 5mm, you'd have to remove the projections that depend on the imported extrusion chunk from the beginning of the file, then change any dimensions which break.  All this is a skill.

I think someone had done this on the Voron Discord; I'd suggest searching there first.

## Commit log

2022-01-24 First public release
    [General_001_Left_Front_Bottom_Right_Rear_Bottom_Clip_x2.stl, General_001_Left_Front_Top_Right_Rear_Top_Clip_x2.stl, General_001_Left_Rear_Bottom_Clip_x1.stl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]
2023-03-06 v3 release
    [General_001_Left_Front_Bottom_Right_Rear_Bottom_Clip_x2.stl, General_001_Left_Front_Top_Right_Rear_Top_Clip_x2.stl, General_001_Left_Rear_Bottom_Clip_x1.stl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]
